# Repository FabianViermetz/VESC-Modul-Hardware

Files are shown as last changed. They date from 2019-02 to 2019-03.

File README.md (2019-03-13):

# VESC6 - Micro-Module
The VESC 6 Module is a small electronics-only platform that is compatible with the VESC firmware. It contains all mandatory electronics and can be combined with a wide range of mosfets and current sensing configurations.

## Electronical Features
- 3S to 12S LiPo support (14S absolute maximum)
- 5V 500mA
- 3.3V 100mA
- 3.3V 25mA low noise analog reference for precise analog readings
- USB, UART, CAN, ADC, PWM interface support (as the original VESC 6)
- Hall Sensor and SPI Encoder support via HALL1,2,3 pins

## Mechanical Features
- **18x30mm** small size
- 4 layers
- castellated pads for best solderability and space usage

Top View:
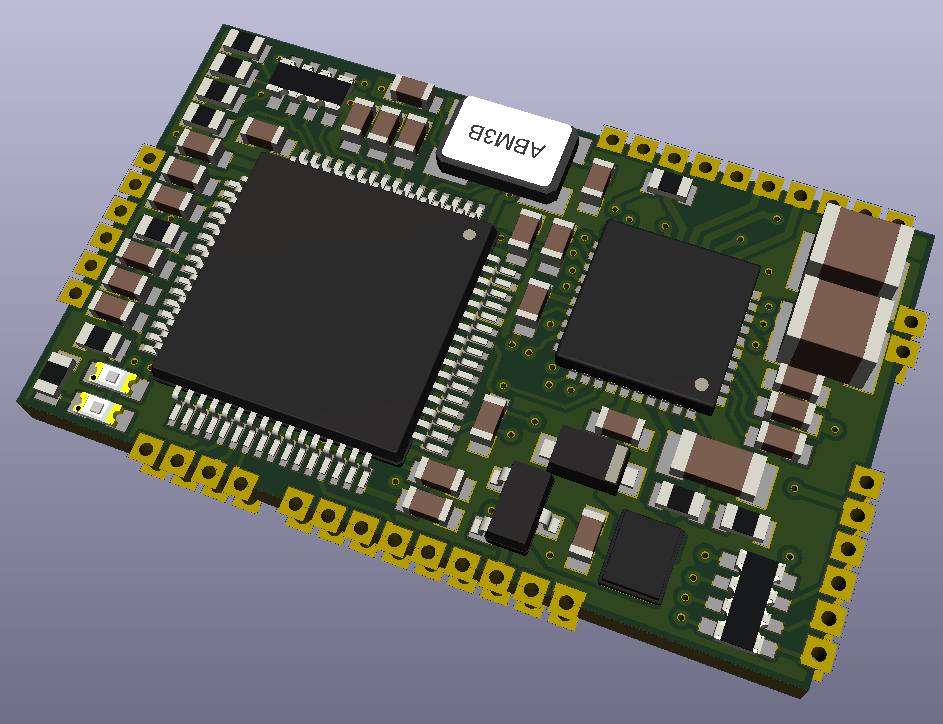
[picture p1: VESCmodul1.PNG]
Top View

Bottom View:
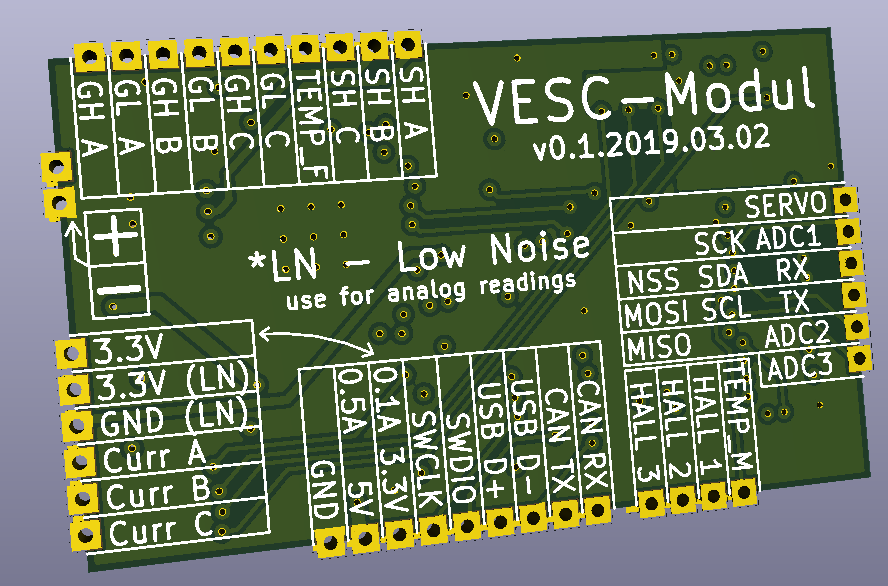
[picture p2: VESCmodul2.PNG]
Bottom View


Next to the STM32F405RGT, the DRV 8320RS is used for driving the 3-Phase-Inverter. 
the Board features all voltage deviding and filtering hardware, so the user only needs to connect the inputs and outputs of the modul to the required peripherals respectively.

**this board is still in development and needs to be tested**

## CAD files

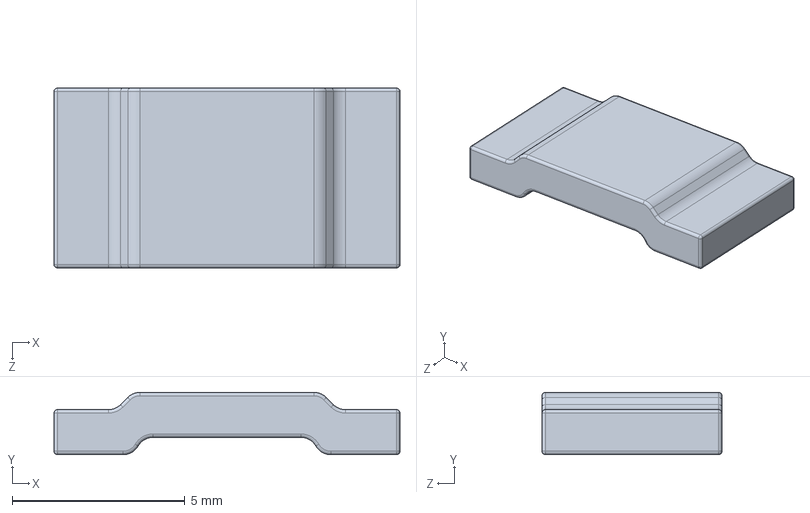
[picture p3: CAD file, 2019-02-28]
MINI4/3dmodels/3921_RESISTOR.STEP
10.0 x 1.80 x 5.20 mm

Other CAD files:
MINI4/3dmodels/user library-pqfn 5x6.wrl.sldprt
MINI4/3dmodels/pqfn 5x6.wrl.sldprt

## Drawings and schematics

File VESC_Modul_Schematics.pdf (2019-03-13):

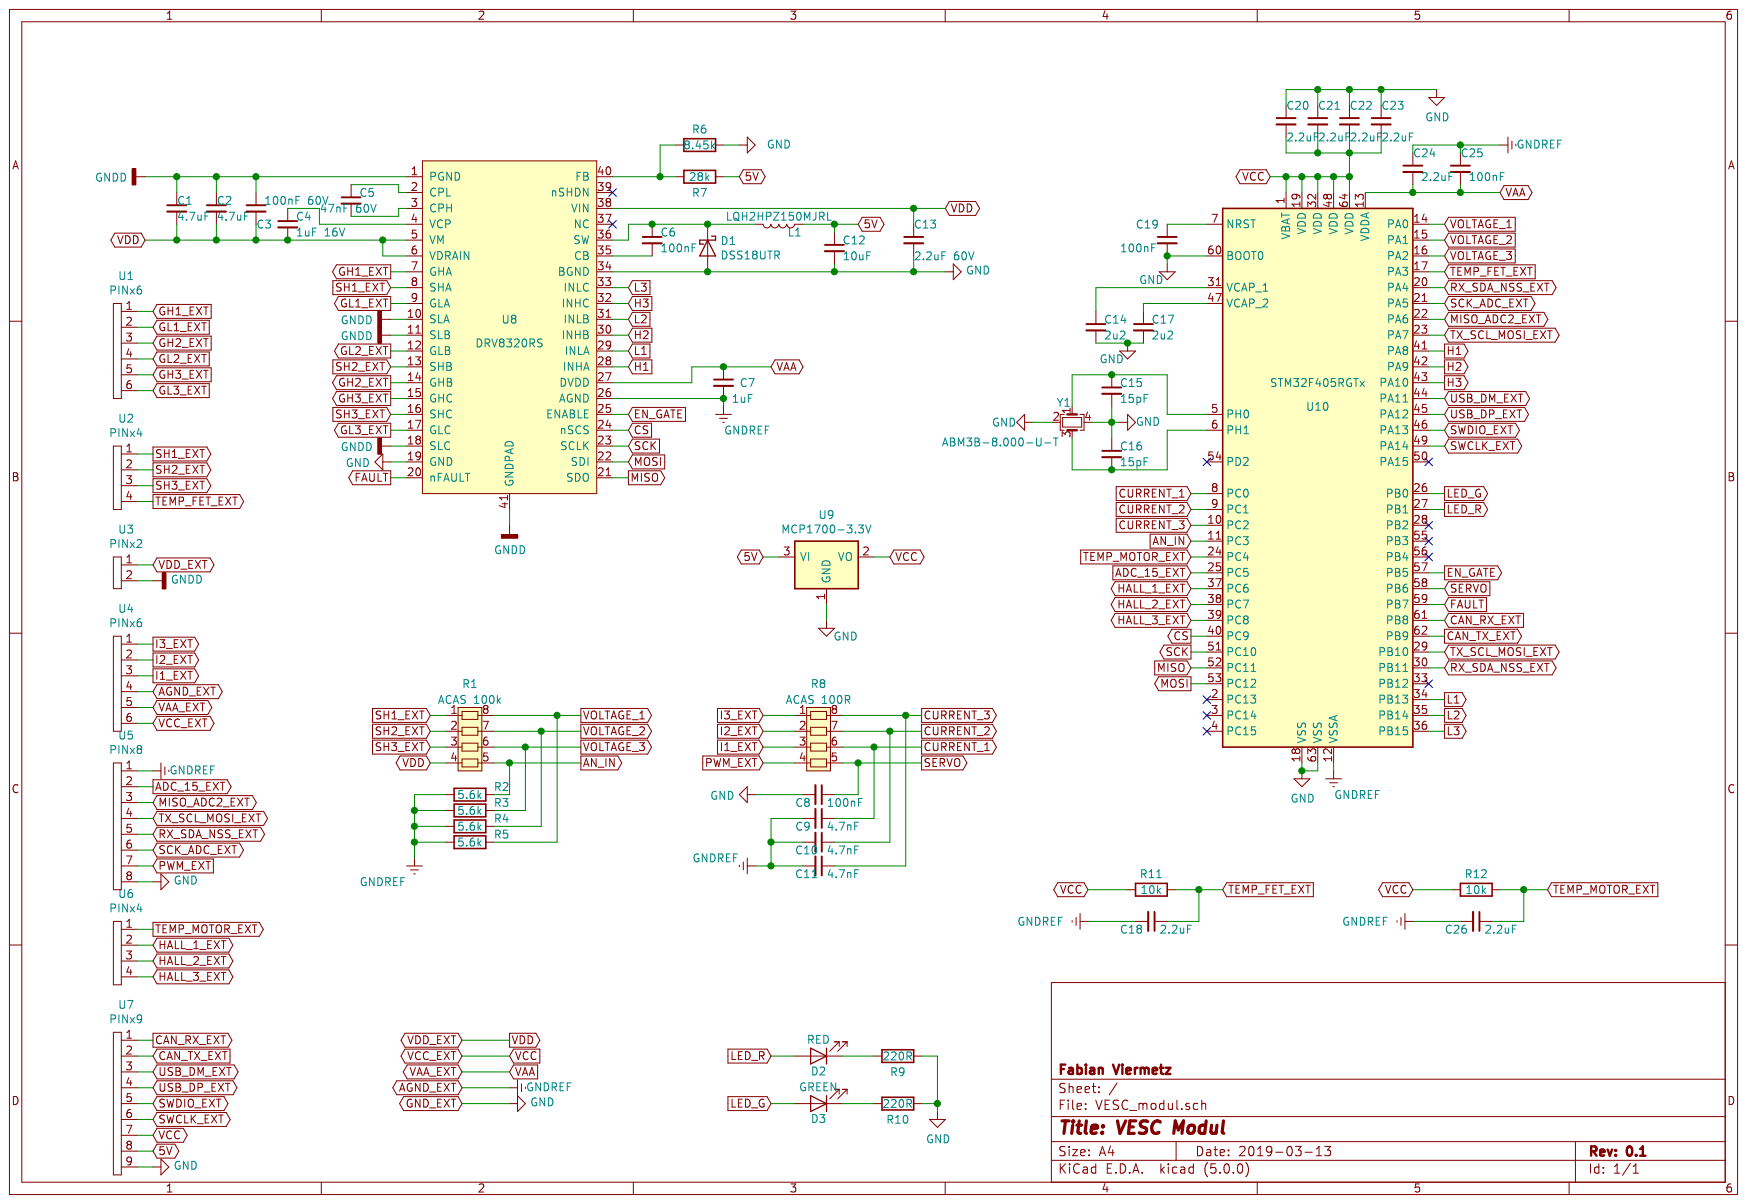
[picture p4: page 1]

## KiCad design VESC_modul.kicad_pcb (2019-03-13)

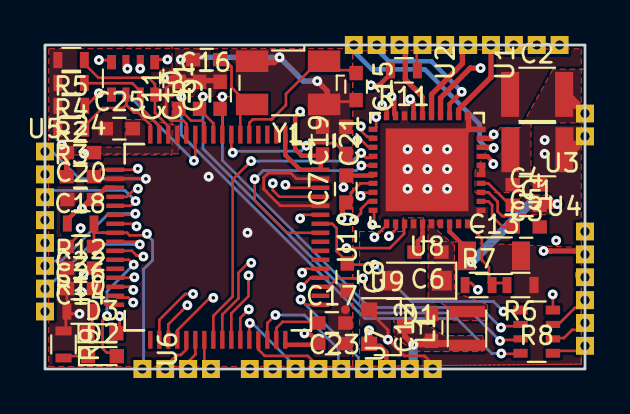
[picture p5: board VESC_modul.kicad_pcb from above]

Board: 4 copper layers, 30.0 x 18.0 mm, 53 parts (0 on the bottom side), 71 nets.

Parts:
C1, C2: 4.7uF; C_1210
C3: 100nF 60V; C_0603
C4: 1uF 16V; C_0603
C5: 47nF 60V; C_0603
C6, C8, C19, C25: 100nF; C_0603
C7: 1uF; C_0603
C9, C10, C11: 4.7nF; C_0603
C12: 10uF; C_0603
C13: 2.2uF 60V; C_1206
C14, C17: 2u2; C_0603
C15, C16: 15pF; C_0603
C18, C20, C21, C22, C23, C24, C26: 2.2uF; C_0603
D1: DSS18UTR; D_SOD-123F
D2: RED; LED_0603
D3: GREEN; LED_0603
L1: LQH2HPZ150MJRL; L_1008
R1: ACAS 100k; R_Array_Convex_4x0603
R2, R3, R4, R5: 5.6k; R_0603
R6: 8.45k; R_0603
R7: 28k; R_0603
R8: ACAS 100R; R_Array_Convex_4x0603
R9, R10: 220R; R_0603
R11, R12: 10k; R_0603
U1, U4: PINx6; PINx6-1.27mm
U2, U6: PINx4; PINx4-1.27mm
U3: PINx2; PINx2-1.27mm
U5: PINx8; PINx8-1.27mm
U7: PINx9; PINx9-1.27mm
U8: DRV8320RS; QFN-40-1EP_6x6mm_Pitch0.5mm
U9: MCP1700-3.3V; SOT-23
U10: STM32F405RGTx; LQFP-64_10x10mm_Pitch0.5mm
Y1: ABM3B-8.000-U-T; Crystal_SMD_Abracon_ABM3B-4pin_5.0x3.2mm

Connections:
5V: C12.1, L1.1, R7.1, U7.8, U9.3
ADC_15_EXT: U5.2, U10.25
AGND_EXT: C7.2, C9.2, C10.2, C11.2, C18.2, C24.1, C25.1, C26.2, R2.2, R3.2, R4.2, R5.2, U4.4, U5.1, U8.26, U10.12
AN_IN: R1.5, R2.1, U10.11
CAN_RX_EXT: U7.1, U10.61
CAN_TX_EXT: U7.2, U10.62
CS: U8.24, U10.40
CURRENT_1: C9.1, R8.6, U10.8
CURRENT_2: C10.1, R8.7, U10.9
CURRENT_3: C11.1, R8.8, U10.10
EN_GATE: U8.25, U10.57
FAULT: U8.20, U10.59
GH1_EXT: U1.1, U8.7
GH2_EXT: U1.3, U8.14
GH3_EXT: U1.5, U8.15
GL1_EXT: U1.2, U8.9
GL2_EXT: U1.4, U8.12
GL3_EXT: U1.6, U8.17
GNDD: C1.1, C2.1, C3.1, U3.2, U8.1, U8.10, U8.11, U8.18, U8.41
GND_EXT: C8.2, C12.2, C13.2, C14.2, C15.2, C16.1, C17.2, C19.2, C20.1, C21.1, C22.1, C23.1, D1.2, R6.1, R9.1, R10.1, U5.8, U7.9, U8.19, U8.34, U9.1, U10.18, U10.60, U10.63, Y1.2, Y1.4
H1: U8.28, U10.41
H2: U8.30, U10.42
H3: U8.32, U10.43
HALL_1_EXT: U6.2, U10.37
HALL_2_EXT: U6.3, U10.38
HALL_3_EXT: U6.4, U10.39
I1_EXT: R8.3, U4.3
I2_EXT: R8.2, U4.2
I3_EXT: R8.1, U4.1
L1: U8.29, U10.34
L2: U8.31, U10.35
L3: U8.33, U10.36
LED_G: D3.2, U10.26
LED_R: D2.2, U10.27
MISO: U8.21, U10.52
MISO_ADC2_EXT: U5.3, U10.22
MOSI: U8.22, U10.53
unnamed: C4.1, U8.4
unnamed: C5.1, U8.2
unnamed: C5.2, U8.3
unnamed: C6.1, D1.1, L1.2, U8.36
unnamed: C6.2, U8.35
unnamed: C14.1, U10.31
unnamed: C15.1, U10.5, Y1.1
unnamed: C16.2, U10.6, Y1.3
unnamed: C17.1, U10.47
unnamed: C19.1, U10.7
unnamed: D2.1, R9.2
unnamed: D3.1, R10.2
unnamed: R6.2, R7.2, U8.40
PWM_EXT: R8.4, U5.7
RX_SDA_NSS_EXT: U5.5, U10.20, U10.30
SCK: U8.23, U10.51
SCK_ADC_EXT: U5.6, U10.21
SERVO: C8.1, R8.5, U10.58
SH1_EXT: R1.1, U2.1, U8.8
SH2_EXT: R1.2, U2.2, U8.13
SH3_EXT: R1.3, U2.3, U8.16
SWCLK_EXT: U7.6, U10.49
SWDIO_EXT: U7.5, U10.46
TEMP_FET_EXT: C18.1, R11.1, U2.4, U10.17
TEMP_MOTOR_EXT: C26.1, R12.1, U6.1, U10.24
TX_SCL_MOSI_EXT: U5.4, U10.23, U10.29
USB_DM_EXT: U7.3, U10.44
USB_DP_EXT: U7.4, U10.45
VAA: C7.1, C24.2, C25.2, U4.5, U8.27, U10.13
VCC: C20.2, C21.2, C22.2, C23.2, R11.2, R12.2, U4.6, U7.7, U9.2, U10.1, U10.19, U10.32, U10.48, U10.64
VDD: C1.2, C2.2, C3.2, C4.2, C13.1, R1.4, U3.1, U8.5, U8.6, U8.38
VOLTAGE_1: R1.8, R5.1, U10.14
VOLTAGE_2: R1.7, R4.1, U10.15
VOLTAGE_3: R1.6, R3.1, U10.16

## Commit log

2019-03-02 folder structure reordered
    [3921_RESISTOR.STEP, VESC_modul.kicad_pcb, VESC_modul.sch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]
2019-03-13 improved GND
    [VESC_modul.kicad_pcb, VESC_modul.sch]
